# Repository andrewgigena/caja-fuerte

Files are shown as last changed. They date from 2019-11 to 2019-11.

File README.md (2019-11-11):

# 1. Introducción

La idea detrás del proyecto, recae en la necesidad moderna de proteger
información muy valiosa y confidencial. Para que esta información no
termine en manos de personas que no deberían tener acceso en primer
lugar, se busca crear un modelo eficiente, seguro y confiable para la
protección de datos, garantizando al usuario que sus datos u objetos
serán protegidos.

Por ese motivo llegamos a la idea de elaborar una caja fuerte a la que
se pueda tener acceso mediante una contraseña. Esta misma será elaborada
por el propietario y podrá ser cambiada a gusto siempre que lo disponga.
Además de la contraseña de usuario, la caja fuerte tendrá una contraseña
maestra que quedará en las manos de la empresa (grupo del proyecto) para
poder acceder a el interior de la caja en caso de: una contraseña
olvidada por el usuario y fallas en el sistema que necesiten un
reajuste.

La caja dispondrá de una alarma que se activará al ser introducida una
contraseña errónea un total de tres veces alertando al dueño sobre la
situación de sus pertenencias.

## 2. Contenido:
### 2.1. Descripción abreviada del contenido del proyecto

Una caja fuerte accesible mediante una contraseña creada por el
propietario. La programación se ejecutara mediando Arduino, además se
dispondrá de una pequeña pantalla que facilitara al usuario la
interacción con el software de seguridad y una alarma para más seguridad
tratando de cubrir todas las áreas posibles que brinden seguridad a lo
que se quiera guardar en ella.

### 2.2. Integrantes del equipo
Los integrantes pertenecientes al grupo 3º BG serán los siguientes:
Andrew Gigena, Gastón Cabrera y Richard Correa.

### 2.3. Asignaturas involucradas
Las asignaturas involucradas hasta ahora serán analógica y digital, en
el desarrollo del proyecto se evaluara la idea de incluir más materias o
simplemente dejar las ya involucradas.

### 2.4. Cronología del proyecto
En el comienzo del proyecto se pensó en utilizar tres sistemas de
seguridad: protección por huella dactilar, contraseña digital mediante
el teclado y una llave física.

Como computadora central de la caja fuerte utilizamos una Arduino debido
a la versatilidad y tamaño reducido de la misma. Además de que permite
modificar su funcionamiento sobre la marcha.

Tras investigar el coste de los módulos disponibles de huellas
dactilares para Arduino, la idea de utilizar este método de seguridad
fue descartada por exceso de coste.

Entonces esperábamos utilizar la llave física y la contraseña digital,
pero por inconvenientes que mencionaremos más adelante, tuvo que
descartarse la llave física.

Cuando finalizamos que sistema utilizar, nos pusimos manos a la obra con
el diseño de la caja fuerte. Para la construcción de la caja primero se
pensó qué materiales utilizar, en un principio se pensó hacerlo de metal
porque tomamos como referencia los diseños existentes en el mercado.
Pero luego de analizar los costos descubrimos que era mejor utilizar
madera compensada. Tras eso se pensó en la forma de unir las paredes de
la misma y llegamos a la conclusión de unirlas con doce ángulos de
metal.

El lugar donde decidimos comprar los materiales fue en la sucursal de
Sodimac por la proximidad del lugar. En este fue comprado las seis
tablas de madera, que se utilizarían para los lados de la caja y se
compró el doble fondo que es una madera más fina que la de los lados.
También los doce ángulos para unir las maderas previamente mencionados.

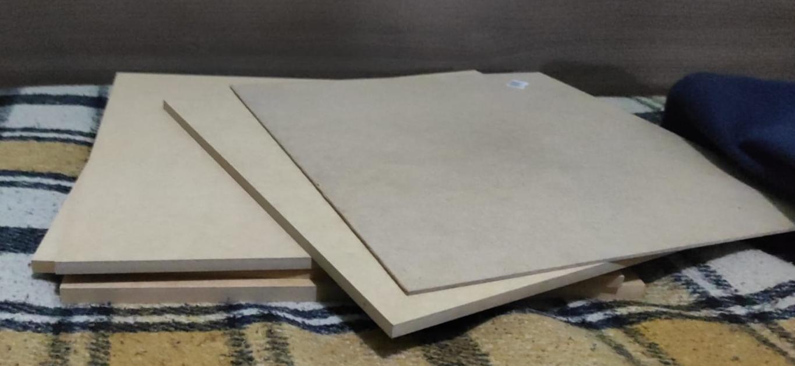
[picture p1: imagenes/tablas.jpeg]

<p align="center"><b>Figura 1. Seis tablas y la tabla del doble fondo</b></p>

Una vez obtenidos los materiales pasamos a construir la caja fuerte.
Primero fue construido el piso y los tres laterales principales. Dejando
a propósito la puerta y el techo para facilitar el acceso y colocación
de los componentes.

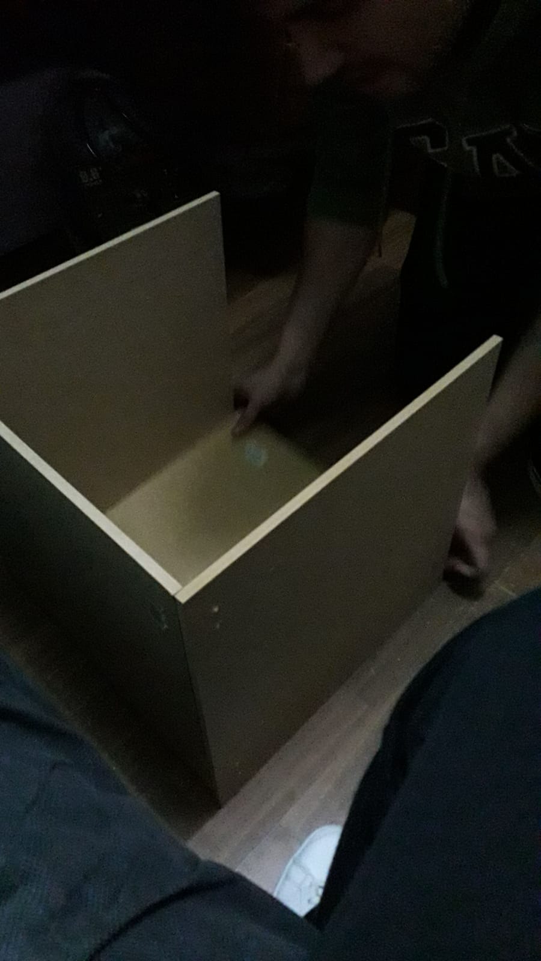
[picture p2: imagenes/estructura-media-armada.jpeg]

<p align="center"><b>Figura 2.  Estructura Inicial</b></p>

En el lapso de dos semanas, investigamos que componentes comprar para
comenzar a programar el proyecto. Fuimos comprando por partes y
avanzando en la programación de ese componente, a pesar de no tener
físicamente el mismo.

Se comenzó utilizando una Arduino Uno para realizar todo el desarrollo,
pero pronto se hizo evidente que el numero de pines seria un problema
para controlar tantos componentes simultáneamente. Por eso se decidió
comprar dos Arduino Mega, una clásica que se utilizaba para realizar
pruebas y otra de tamaño reducido pensada para ser soldada.

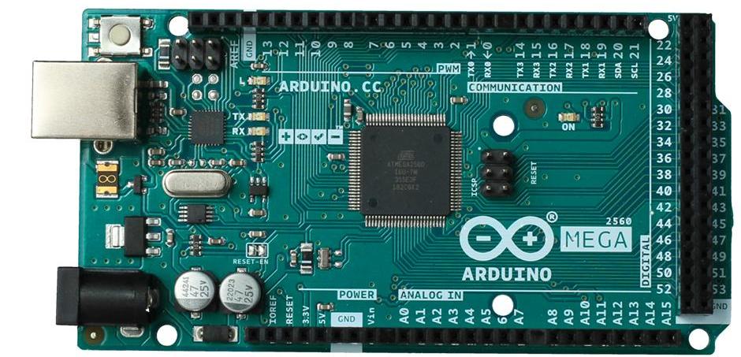
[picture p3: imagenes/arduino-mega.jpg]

<p align="center"><b>Figura 3.  Arduino Mega Clásica</b></p>

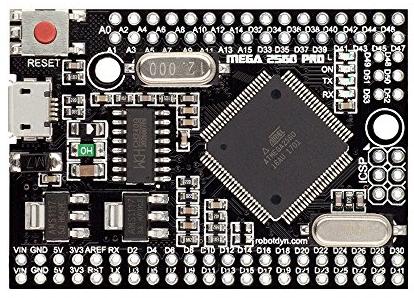
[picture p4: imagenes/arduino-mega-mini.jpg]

<p align="center"><b>Figura 4.  Arduino Mega Mini</b></p>

Durante la espera de los envíos internacionales, fue diseñada y
ensamblada la placa con la iluminación led que se encargara de mostrar
los intentos disponibles, y si la caja estaba abierta o cerrada.


<p align="center"><b>Figura 5.  Iluminación de ledes</b></p>

Mientras se buscaba un teclado acorde al proyecto, se hizo uno de
prueba, tras la compra del teclado de membrana su implementación a la
caja fue inmediata.


<p align="center"><b>Figura 6.  Teclado de prueba</b></p>

Tras solucionar el asunto de la Arduino, continuamos con modelado de la
caja. Nos enfocamos en el calado de la puerta donde iría la pantalla y
los ledes. Las medidas del calado de la pantalla son de 7.5 x 2.5cm,
luego los orificios de los ledes los hicimos con una mecha de 7mm, el
calado de la puerta lo hicimos con un cincel.

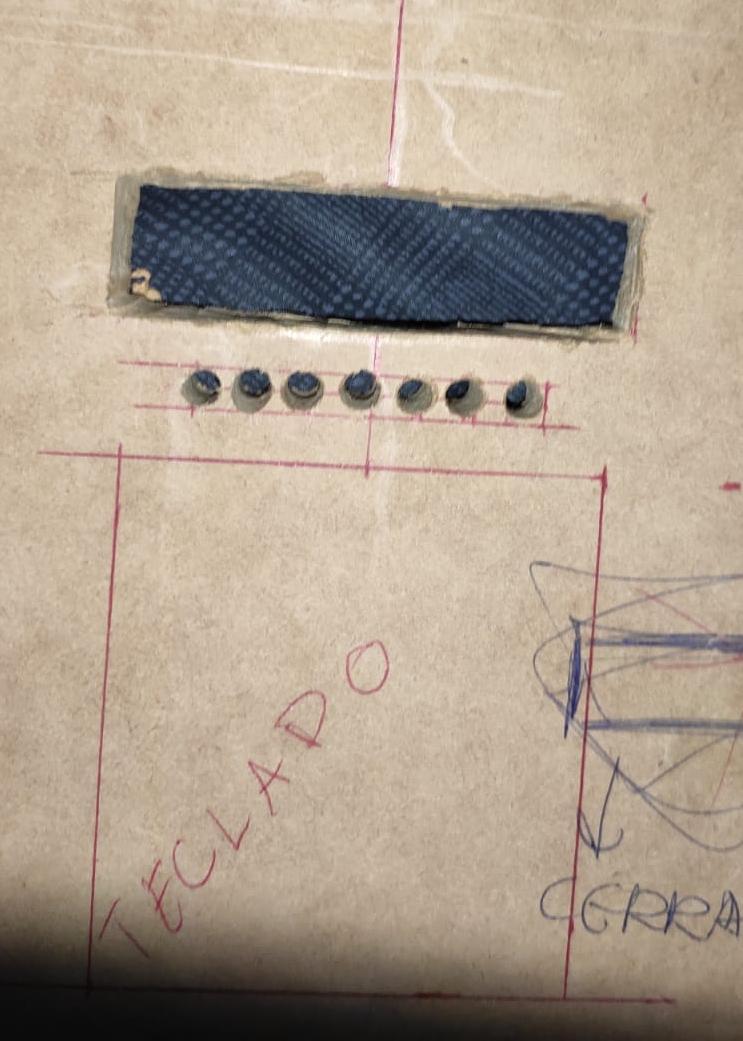
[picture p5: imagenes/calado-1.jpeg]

<p align="center"><b>Figura 7.  Calado de Ledes/Pantalla</b></p>

Aquí es cuando notamos un error que nos llevo a descartar la llave
física, que impedía la colocación de la cerradura y perjudicaba la
estructura de la puerta.

Dentro de las compras tanto locales como internacionales, se encuentra
la pantalla, pensada como el medio principal de interacción que tendría
el usuario con el sistema.

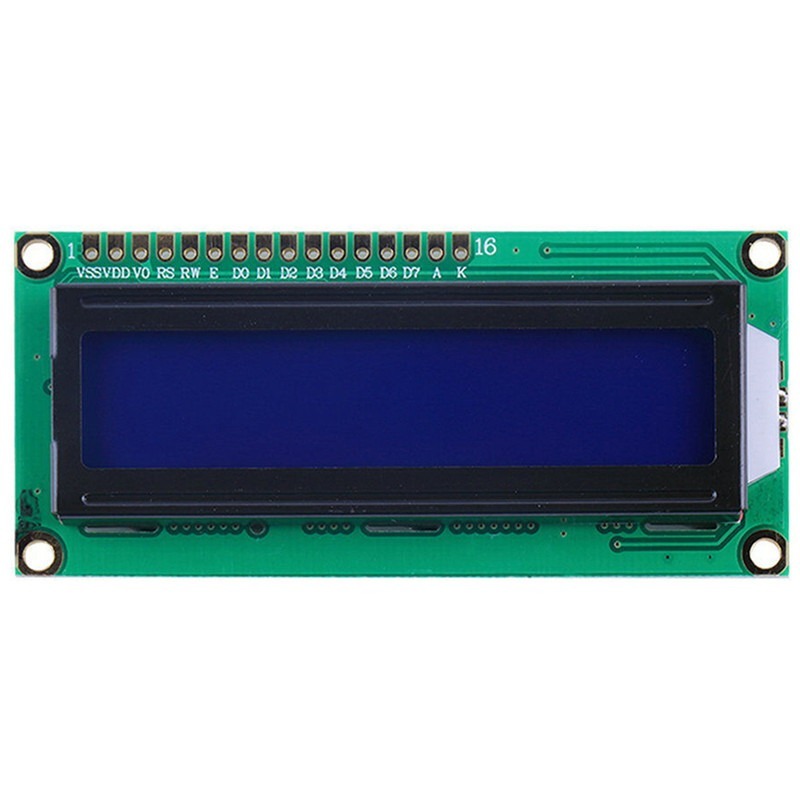
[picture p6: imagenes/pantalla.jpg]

<p align="center"><b>Figura 8.  Pantalla LCD</b></p>

El teclado de membrana previamente mencionado como suplente al teclado
de botones.


<p align="center"><b>Figura 9.  Teclado de membrana</b></p>

Luego fue comprada la cerradura para comprobar que el orificio de la
cerradura en la puerta coincidiera, luego de llegar a un diseño
satisfactorio, fue implementado el código de la cerradura que seria
controlado por un relé.


<p align="center"><b>Figura 10. Cerradura Electromagnetica</b></p>

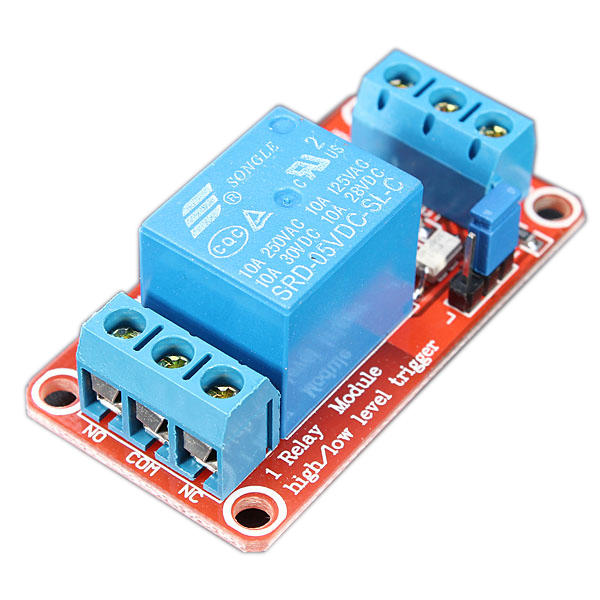
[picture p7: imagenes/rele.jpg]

<p align="center"><b>Figura 11. Relé</b></p>

Cuando todos los componentes estaban físicamente disponibles, realizamos
todas las pruebas de código y terminamos la puerta, fueron colocados
todos los componentes en la puerta para ser soldados y/o
interconectados.

Una vez realizado el calado en la puerta faltante y la colocación de los
componentes en la misma, procedimos a ensamblarla en la estructura.

Decidimos que la puerta quedaría colocada entre los laterales de la
caja. Para hacer esto, utilizamos dos bisagras, qué estarían colocados a
la derecha de la caja fuerte, una vez colocada la puerta procedimos a
colocar el asa, que mejor se acoplaba al diseño de la caja fuerte.
Colocamos el techo de la caja fuerte del mismo modo que colocamos los
laterales y el piso. Se hizo un calado dónde iría la entrada de
corriente, ubicada en la parte posterior de la caja y agujeros donde
estarían ubicados los parlantes de la alarma, estos últimos fueron
hechos con una mecha de 5mm.

Colocamos la entrada de corriente de 230v interconectada a una fuente
conmuta de 20v, en la salida de esta fue conectado un regulador de
voltaje LM317 para bajar el voltaje a 12v.

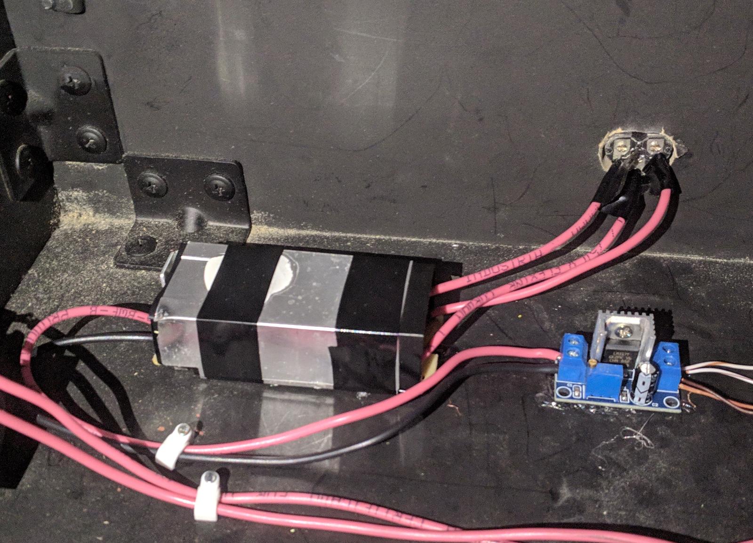
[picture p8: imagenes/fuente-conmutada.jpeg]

<p align="center"><b>Figura 12. Fuente Conmutada y Regulador de Voltaje</b></p>

***Falta el amplificador y el rele del mismo***

La caja fuerte fue pintada progresivamente mientras se avanzaba e la
misma. El color escogido fue negro mate ya que notamos que era el color
más frecuente en el mercado de las cajas fuertes, para que luzca más
estético y profesional.


<p align="center"><b>Figura 13. Caja Fuerte terminada</b></p>

### 2.5 Complicaciones durante en producción
---------------
#### 2.5.1 Complicaciones en la programación

Durante la programación, fue necesario utilizar la EEPROM de manera
obligatoria, cada vez que inicia la caja comprueba diferentes valores
para impedir el uso o saltarse la programación para abrir la puerta.

\
Otra dificultad que ocurrió durante la programación fue impedir todos
los errores que imposibilitarían el inicio o continuación de la misma.
Eso fue realizado mediante distintos modos internos que el programa
accedería, por ejemplo el modo de nuevo pin. Este modo que se accede con
el único propósito de cambiar el pin actual o fijar uno inicial.

Los modos internos utilizados por el programa son los siguientes:

-   **Modo Alarma:** La alarma comienza a sonar y el usuario/empleado de
    la empresa debe colocar el código puk para desactivar la alarma y
    volver al Modo Ingreso de Pin
-   Modo Nuevo Pin: A través del teclado permite ingresar un pin que se
    guardara en la EEPROM como el pin almacenado. El usuario puede
    aceptar el pin que ingreso o volver a ingresar otro.
-   **Modo Ingreso de Pin:** El usuario debe ingresar el pin de seis
    dígitos. Tras confirmar, el sistema compara el pin ingresada con el
    pin almacenado, si la contraseña es correcta el sistema entra en el
    Modo Caja Abierta. Si en cambio, el pin es incorrecto restaría un
    intento y desactivaría un led de intentos. Cuando los intentos son
    iguales a cero el sistema se bloqueara para entrar en el Modo
    Alarma.
-   **Modo Caja Abierta:** Al iniciar este modo toma el tiempo de inicio
    para calcular posteriormente que hayan transcurrido cinco minutos.
    Pasados estos cinco minutos la cerradura automáticamente se
    cerraría. A pesar de esto, el usuario puede cerrar a voluntad la
    cerradura y cambiar el pin
-   Modo Programador: Permite modificar aspectos de la caja a traves de
    comandos especiales. Estos comandos son desactivar/activar la
    alarma, desactivar/activar cerradura, desactivar/activar primer
    inicio.

#### 2.5.2 Complicaciones de ensamblaje

Mientras realizamos la construcción de la caja obtuvimos una serie de
problemas, estos problemas fueron:

-   Al colocar las bisagras en la puerta, esta no se abría
    completamente. Por eso nos vimos obligados a alterar un poco el
    diseño de la misma, la solución que encontramos a este problema fue
    agregarle un complemento al lateral donde iban las bisagras y
    también sé lijo un ángulo de la puerta. Estos cambios son para
    mejorar la apertura de la puerta.

-   Otro de los problemas que tuvimos fue en la parte de la colocación
    de los laterales ya que la madera era compensada y al colocar los
    tornillos no apretaban lo suficiente. Este problema lo solucionamos
    con unos tornillos que se acoplan mejor a la madera compensada y
    también se trató de no quitar los tornillos una vez colocado en la
    madera.
-   El calado de la pantalla tuvo que ser movido unos centímetros hacia
    arriba, porque la pantalla y la iluminación led se solapaban las
    placas e impedía colocarlos correctamente.

Durante la colocación de los componentes tuvimos problemas con la
sección de los cables, estos cables se partieron y que tuvieron que ser
resoldados.

#### 2.5.3 Complicaciones en la soldadura

Se utilizo un estaño de mala calidad durante el comienzo de la
soldadura, con un alto grado de plomo. Esto nos obligo a cambiar por un
estaño de más calidad.

También tuvimos un cortocircuito que daño la pantalla LCD, este fue
producido por cables multifilares mal soldados, algo que nos obligo a
comprar otra y repensar como conectar las soldaduras para que no ocurra
lo mismo.

Al final notamos que una gota de estaño cayo en los pines del ATMEGA
2560 de la Arduino Mega, y tuvo que ser resoldado el chip SMD con mucho
cuidado para evitar cortocircuitar el integrado.

# 3. Comportamiento del sistema

## 3.1 Diagrama de bloques:
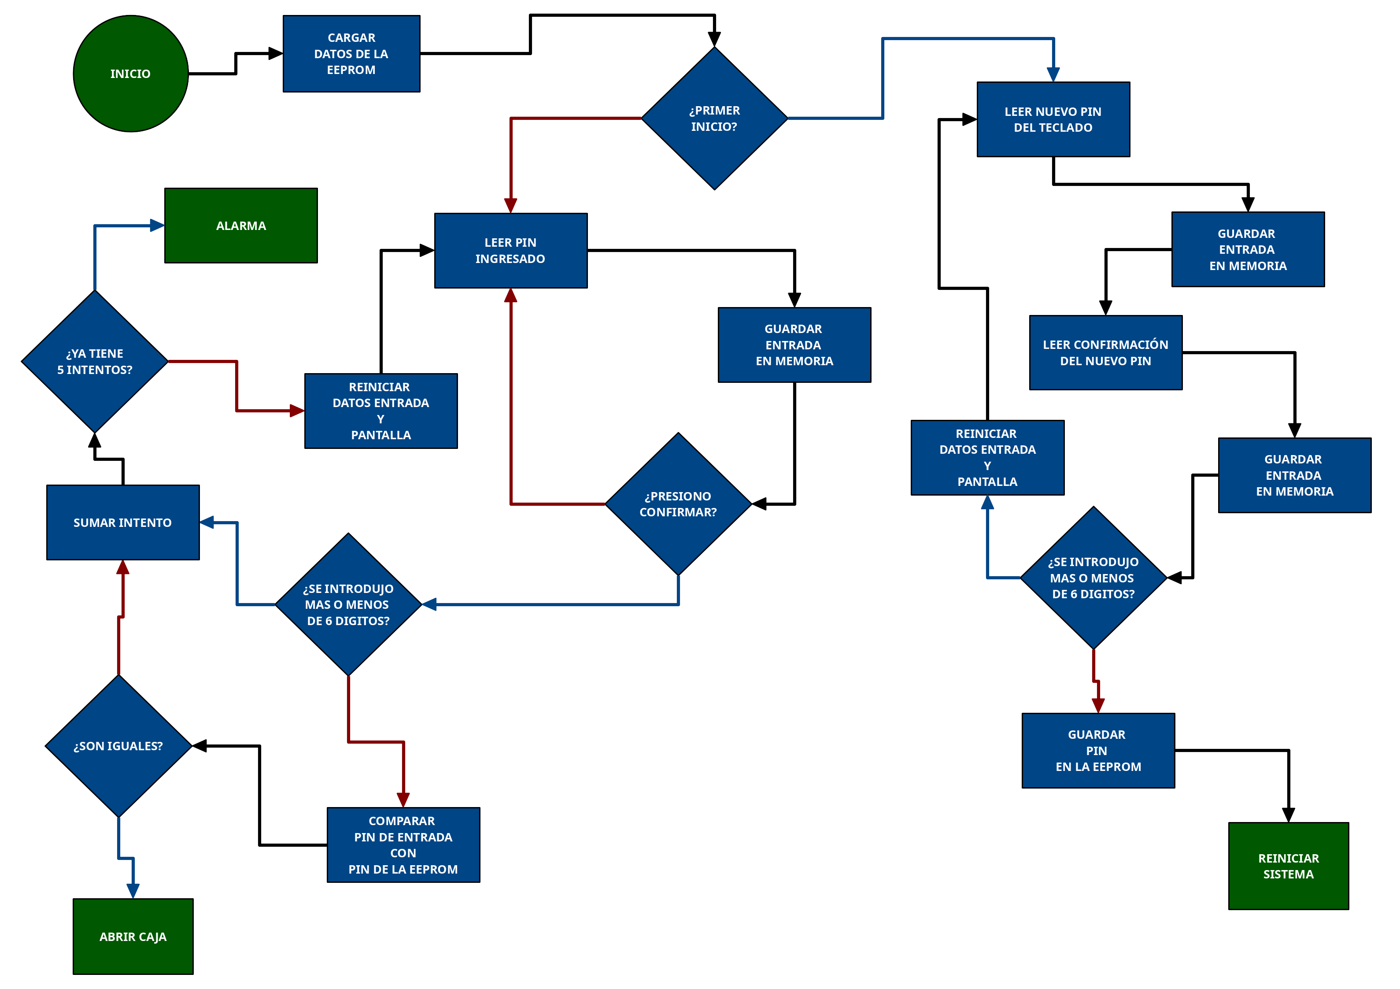
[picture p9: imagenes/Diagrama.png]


## 3.2 Comportamiento Funcional:
El programa dispone de dos modos principales, el modo usuario donde se
realizara casi todas las operaciones y el modo programador/empresa donde
hacen cambios de pruebas/funcionamientos.

### 3.2.1 Modo usuario:

Al inicio del sistema este comprueba si este es el primer inicio del
mismo. Si la respuesta es positiva, pide un nuevo pin de seis dígitos al
usuario. Luego pide una confirmación de la misma para guardar en la
EEPROM o reingresar otra contraseña distinta. En el caso de tener un pin
ya designado, se deberá ingresar el misma para acceder al interior de la
caja.

El usuario tiene cinco intentos para ingresar correctamente el pin
guardado, donde por cada intento fallido se apagará uno de los ledes de
intentos. En el caso de ocurrir cinco intentos fallidos, se encenderá un
led encendido de color rojo y se activara una alarma para alertar al
usuario de un posible intruso. La alarma seguirá activa hasta que la
empresa o el usuario ingrese el código puk.

En caso de ingresar el pin correcto, se encenderá un led de color verde,
se reinicia el número de intentos disponibles a cinco, y se accionara la
cerradura para tener el acceso a la caja fuerte.

Tras acceder a la caja fuerte, el usuario podrá almacenar o retirar el
contenido del mismo. También podrá cambiar la contraseña actual y/o
cerrar la puerta manualmente. Aun así está habilitado un sistema de
cerrado automático tras cinco minutos

### 3.2.2 Modo programador:

En este modo es accesible mediante a una pin especial que solo tendrá
conocimiento la empresa, en este modo se podrá: Tanto activar o
desactivar la alarma, abrir o cerrar la caja y cambiar la contraseña del
usuario, luego de finalizado estos procedimientos se saldrá del modo
programador para ingresar nuevamente al modo usuario, donde se activarán
la funciones asignadas.

# 4. Descripción de los componentes

## 4.1. Arduino Mega

## 4.2. Teclado
El teclado utilizado es uno de membrana de 12 botones en una
organización de 4 filas x 3 columnas. Es muy utilizado con las placas de
desarrollo Arduino, sensible al tacto por lo cual no se requiere una
gran presión para activar las teclas lo cual lo vuelve muy cómodo, la
ventaja de este teclado es que al tener una conexión flexible puede ser
colocado en cualquier superficie sin problemas.

## 4.3. Parlantes
Se utilizaron dos parlantes de 4Ω en serie, debido a que era lo
que más nos convenía en relación tamaño y potencia. Este dispositivo
esta destinado a la conversión de ondas eléctricas en energía mecánica
y de mecánica en acústica. Es por tanto la puerta por donde sale el
sonido al exterior desde los aparatos que posibilitaron su
amplificación.

## 4.4. Cerradura
Se utilizo esta cerradura por su tamaño reducido y voltaje ya que se
acciona con 12v. Este voltaje es compatible con el amplificador que
utiliza 12v algo conveniente para el proyecto. La cerradura está
compuesto por un solenoide, que es básicamente un electromagneto.

Estos están hechos de una gran bobina de alambre con una armadura (un
lingote de metal) en el medio. Cuando la bobina es energizada, el
lingote es tirado al centro de la bobina. Esto hace que el solenoide sea
capaz de empujar hasta el final de la cerradura.

Normalmente el lingote está expandido por lo tanto no puedes abrir la
puerta porque obstruye el camino. No usa ninguna potencia extra en este
estado. Cuando son aplicados 9-12VDC, el lingote se retrae por lo que no
sobresale más y la puerta puede ser abierta. Los solenoides vienen con
un lingote inclinado como se muestra, pero puedes abrirlo con los dos
tornillos de cabeza Philips y rotarlo 180 grados, por lo que podrán
coincidir con la puerta que quieras usarlos.

## 4.5. Pantalla
Utilizamos esta pantalla por ser muy compatible con la Arduino debido a
las librerías y ejemplos ya existentes. Esta pantalla es de 16x02
caracteres y opera con un voltaje de 5v. Tiene una interfaz paralela de
4 u 8 bits, nosotros utilizamos la segunda interfaz. Su color de texto
es blanco y la luz de fondo es de color azul.

## 4.6. Regulador de Voltaje
Utilizamos un regulador de voltaje porque la fuente es de 20v y
necesitamos reducir a 12v debido a que nuestro circuito funciona a este
voltaje. Para ello utilizamos un LM317, qué permite regular el voltaje
de entrada hacia un máximo de 1.5A y 37V de salida.

## 4.7. Amplificador
Usamos un amplificador de audio de 18w para el funcionamiento de los
parlantes de la alarma, ya que este era necesario para mejorar la
potencia del audio ya que sin el mismo, el sonido era muy bajo. Este
amplificador utiliza un TDA2030 cuyo rango de operación es de 6v a 18v,
y la salida al parlante de 4Ω a 8Ω

## 4.8. Relés
Se utilizo un relé de 5v porque era compatible con el Arduino y permite
cambiar la polaridad de normalmente cerrado (NC) al normalmente abierto
(NA). Los relés son dispositivos electromagnéticos. Funciona como un
interruptor controlado por un circuito eléctrico en el que, por medio de
una bobina y un electro imán, se acciona un juego de uno o varios
contactos que permiten abrir o cerrar otros circuitos eléctricos
independientes.

## 4.9. Iluminación de Ledes

# 5. Cotización del Proyecto
Las estimaciones de costes que tuvimos al comienzo del proyecto eran de
8500 $U, pero tras comprar todo y armarlo, el presupuesto final fue de
7320 $U, porque algunos productos los trajimos desde el extranjero.
  
 Cantidad | Material                           | Precio
--------- | ---------------------------------- | ---------
  1       | Cerradura electromagnética de 12v  | 1300 $U
  1       | Teclado de 4x3 botones             |  130 $U
  2       | Parlantes de 4Ω                    |  GRATIS
  1       | Arduino Mega 2560 Pro Embedded     |  330 $U
  1       | Pantalla LCD 1602A                 |  240 $U
  1       | Placas de prototipo de puntos      |  GRATIS
  1       | Relé de 5v Control, 220AC Salida   |  160 $U
  4       | 10 metros de cables de 0.5mm       |  320 $U
  7       | Tablones de 40cm x 40cm            | 1120 $U
  2       | Bisagras de hierro                 |   80 $U
  12      | Ángulos de Juntura                 |  720 $U
  2       | Aerosoles de Pintura               |  920 $U
  1       | Rollo de Estaño                    | 1600 $U
  1       | Pestillo                           |   80 $U

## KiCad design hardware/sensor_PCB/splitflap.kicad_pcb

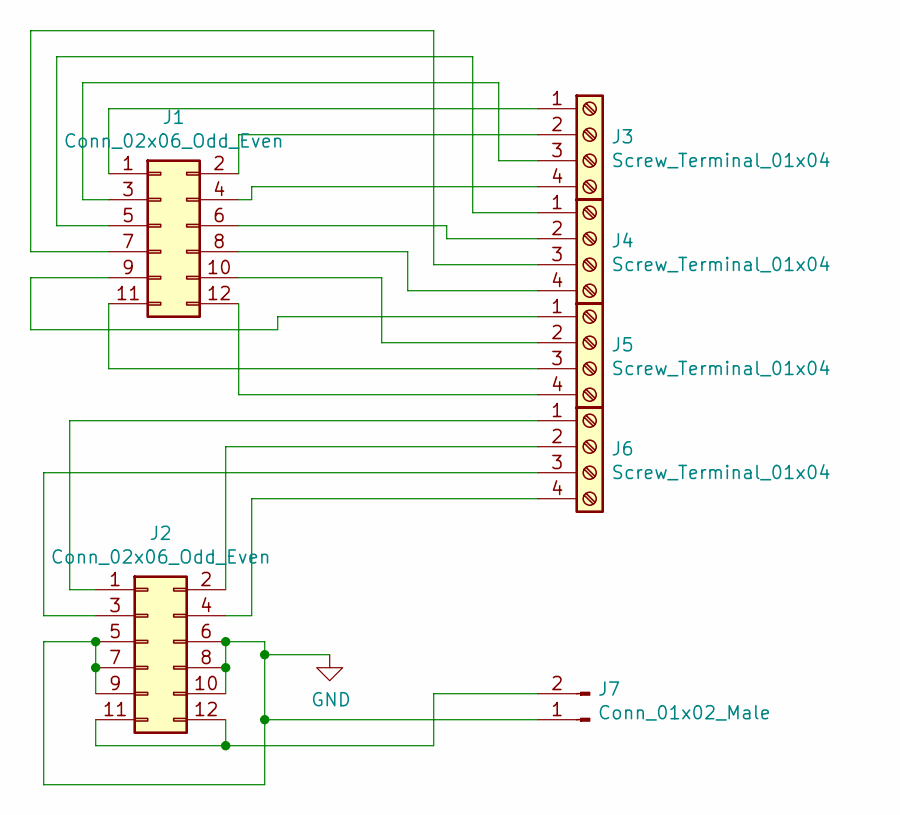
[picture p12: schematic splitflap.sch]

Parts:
J1, J2: Conn_02x06_Odd_Even; IDC-Header_2x06_P2.54mm_Vertical
J3, J4, J5, J6: Screw_Terminal_01x04; TerminalBlock_bornier-4_P5.08mm
J7: Conn_01x02_Male; JST_EH_B2B-EH-A_1x02_P2.50mm_Vertical

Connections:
GND: J2.5, J2.6, J2.7, J2.8, J2.9, J2.10, J7.1
unnamed: J1.1, J3.1
unnamed: J1.2, J3.2
unnamed: J1.3, J3.3
unnamed: J1.4, J3.4
unnamed: J1.5, J4.1
unnamed: J1.6, J4.2
unnamed: J1.7, J4.3
unnamed: J1.8, J4.4
unnamed: J1.9, J5.1
unnamed: J1.10, J5.2
unnamed: J1.11, J5.3
unnamed: J1.12, J5.4
unnamed: J2.1, J6.1
unnamed: J2.2, J6.2
unnamed: J2.3, J6.3
unnamed: J2.4, J6.4
unnamed: J2.11, J2.12, J7.2

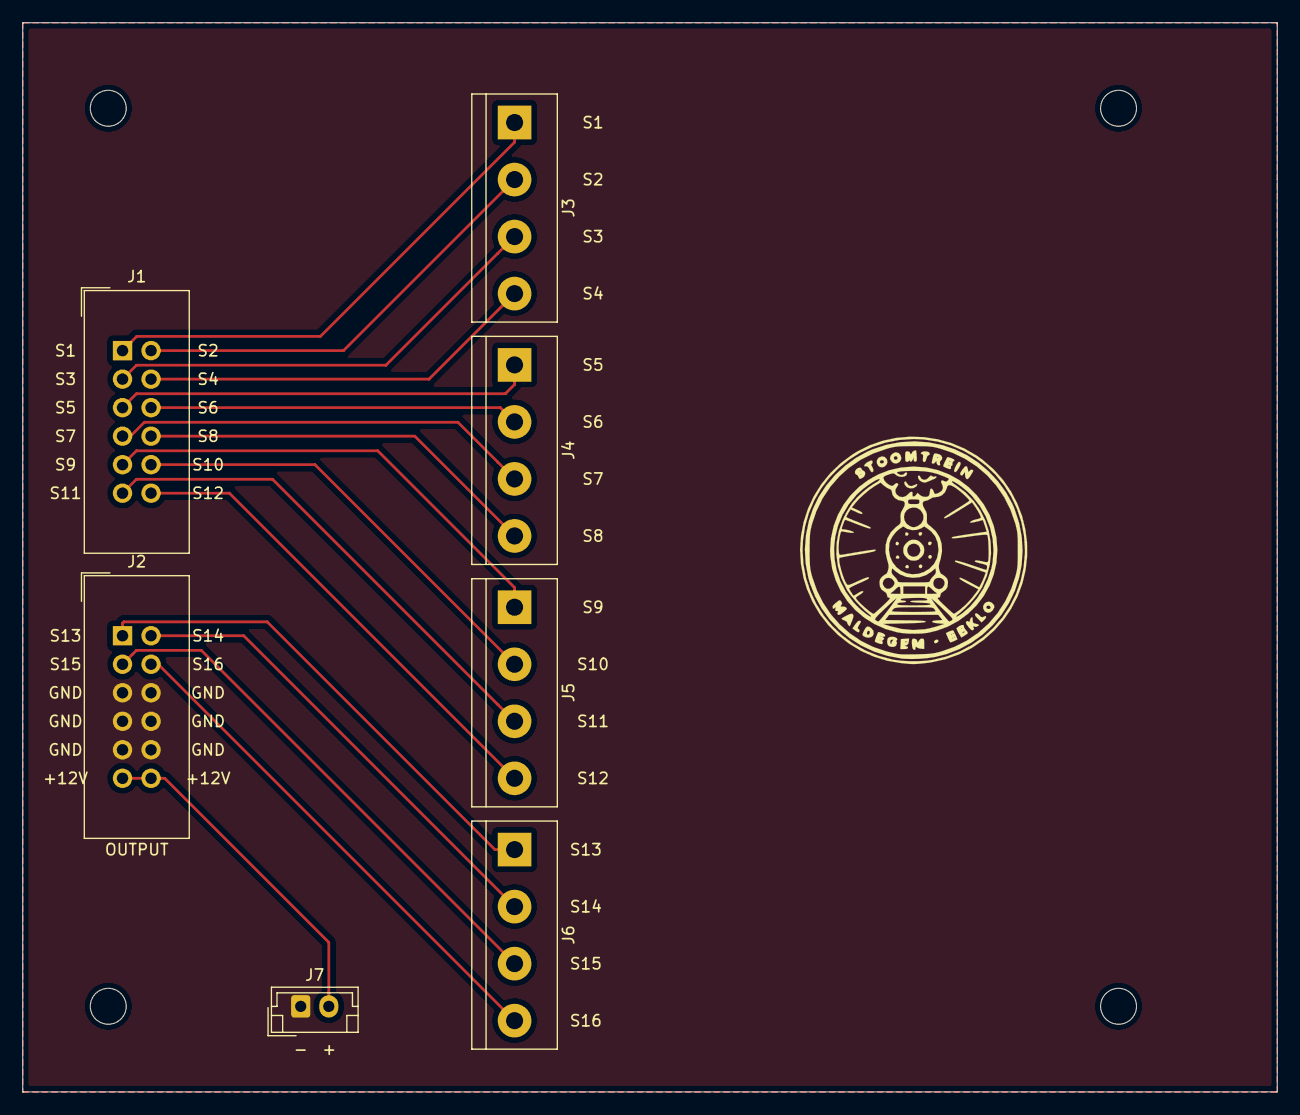
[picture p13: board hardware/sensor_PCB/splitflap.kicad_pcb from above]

Board: 2 copper layers, 111.8 x 95.2 mm, 7 parts (0 on the bottom side), 18 nets.

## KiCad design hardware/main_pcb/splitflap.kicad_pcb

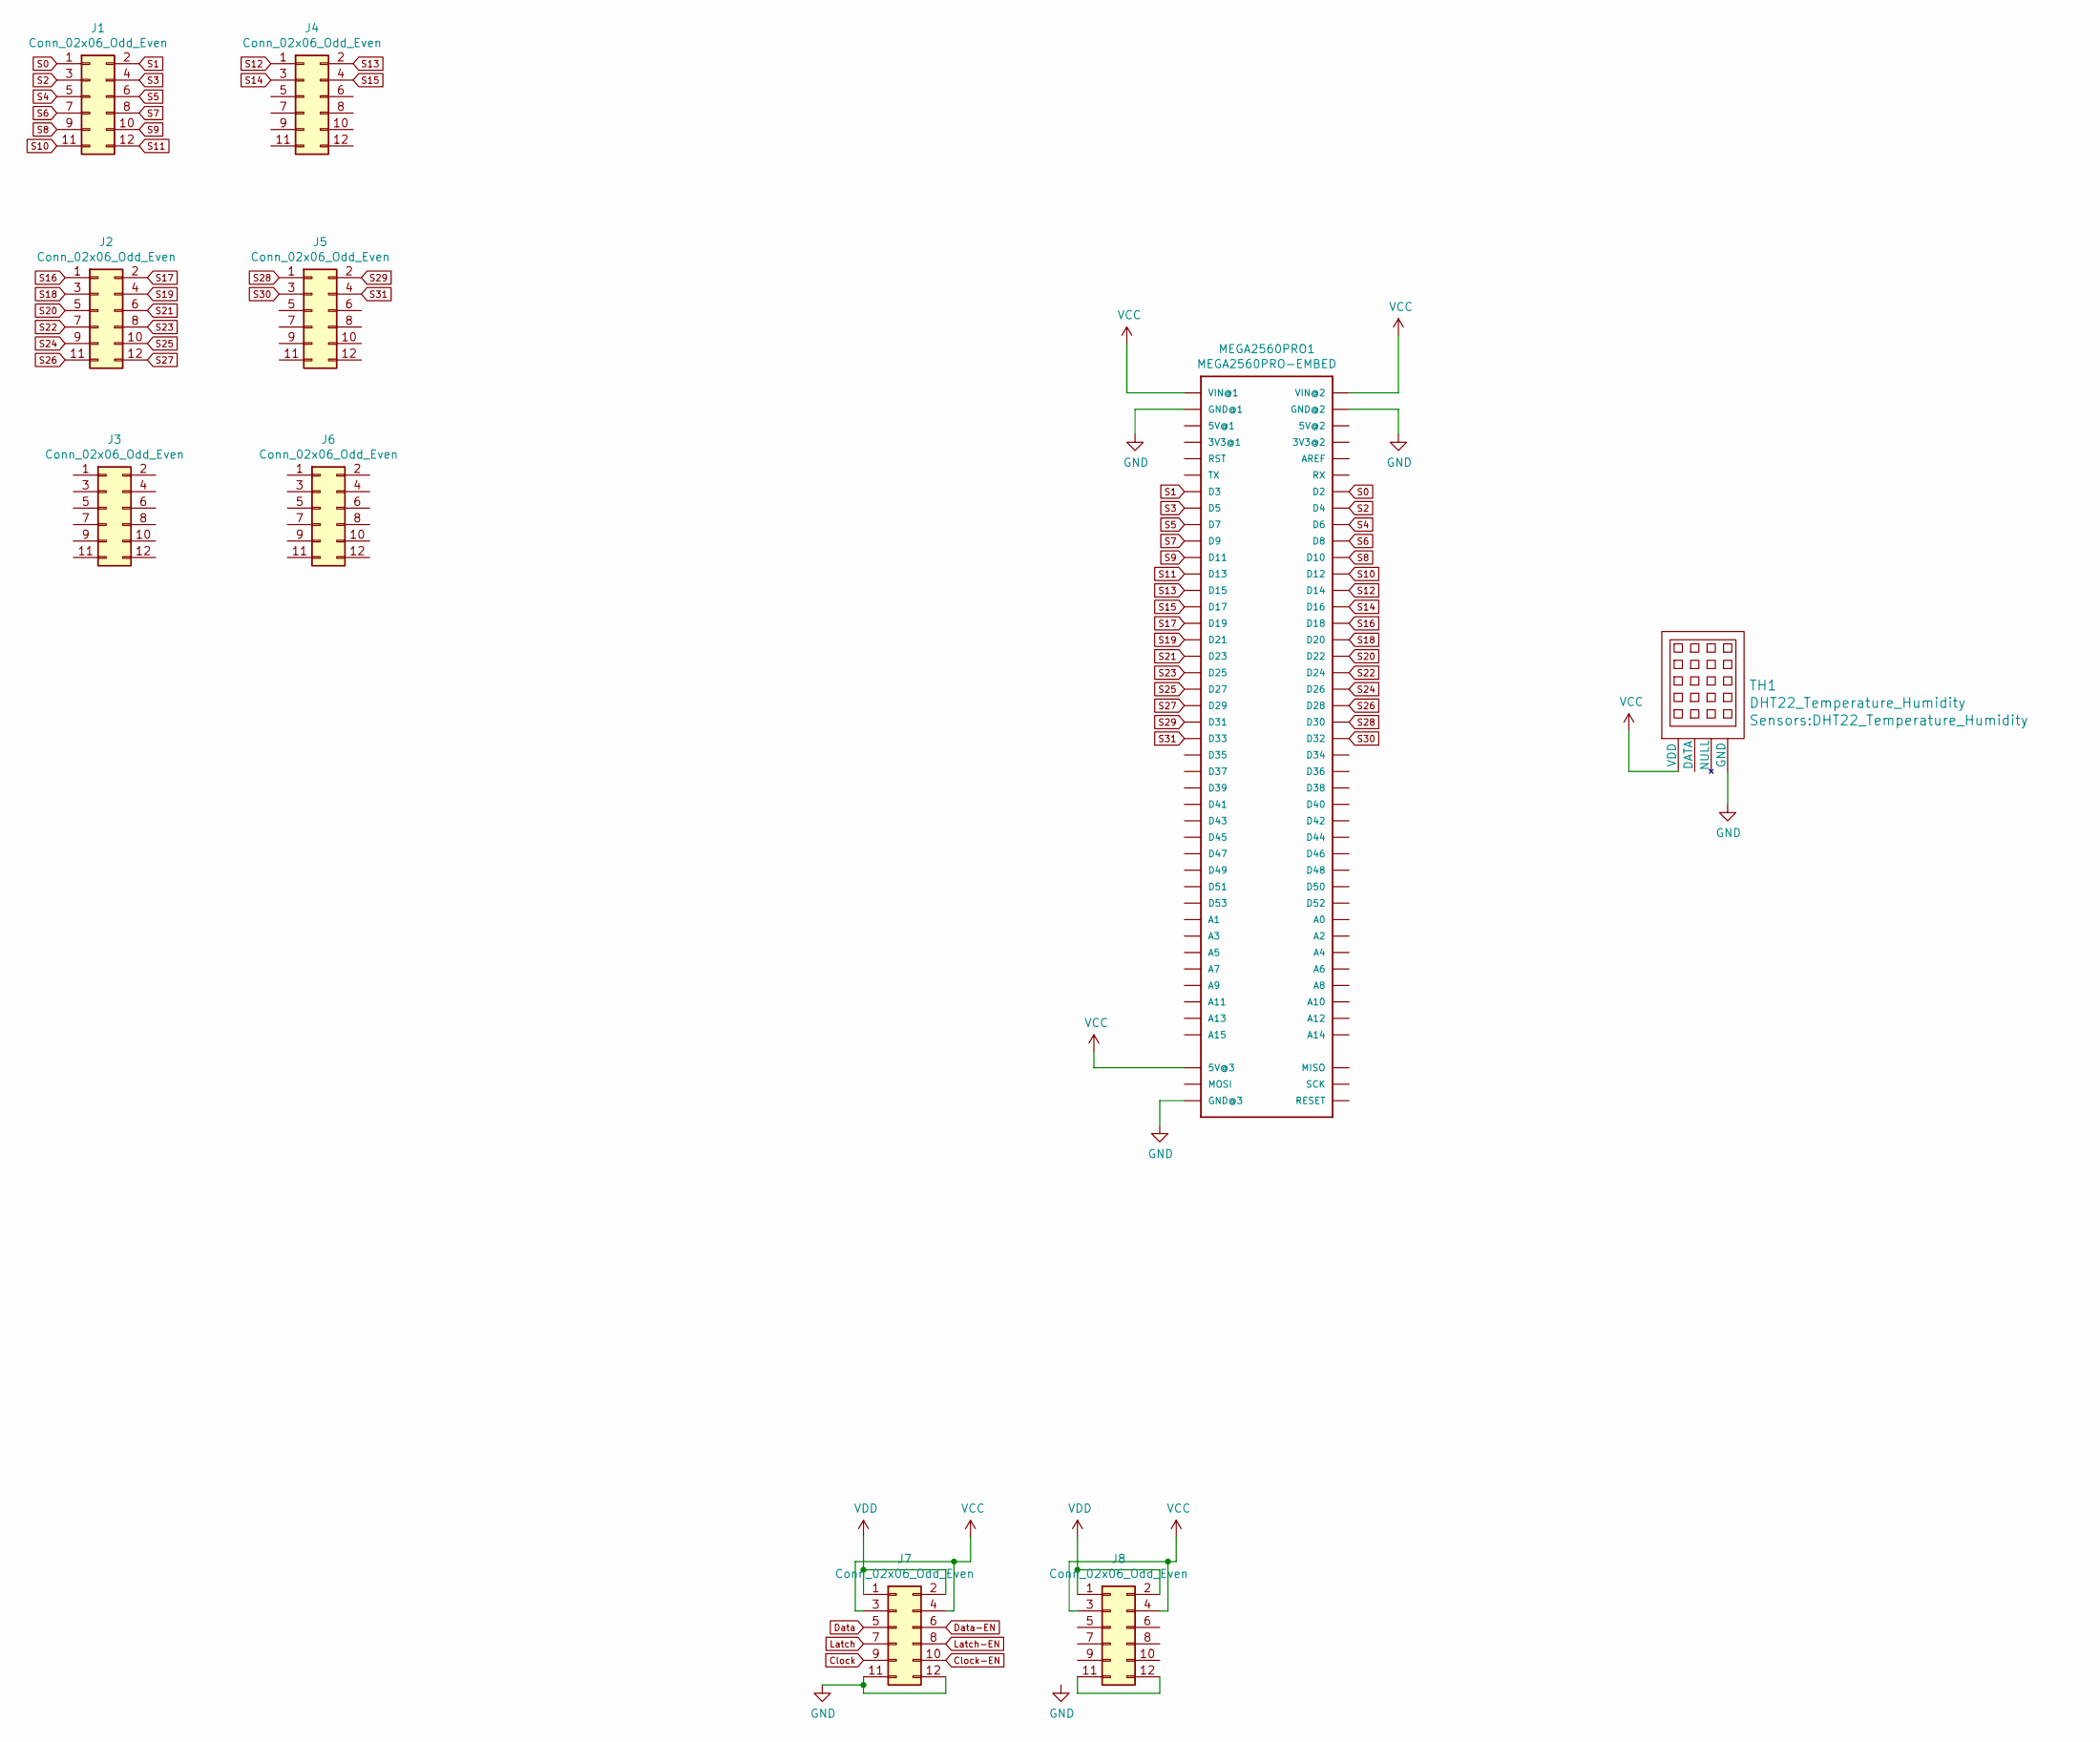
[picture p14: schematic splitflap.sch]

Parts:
J1, J2, J3, J4, J5, J6, J7, J8: Conn_02x06_Odd_Even; IDC-Header_2x06_P2.54mm_Vertical
MEGA2560PRO1: MEGA2560PRO-EMBED
TH1: DHT22_Temperature_Humidity

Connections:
Clock: J7.9
Clock-EN: J7.10
Data: J7.5
Data-EN: J7.6
GND: J7.11, J7.12, MEGA2560PRO1.GND@1, MEGA2560PRO1.GND@2, MEGA2560PRO1.GND@3, TH1.4 (GND)
Latch: J7.7
Latch-EN: J7.8
unnamed: J8.11, J8.12
S0: J1.1, MEGA2560PRO1.D2
S1: J1.2, MEGA2560PRO1.D3
S2: J1.3, MEGA2560PRO1.D4
S3: J1.4, MEGA2560PRO1.D5
S4: J1.5, MEGA2560PRO1.D6
S5: J1.6, MEGA2560PRO1.D7
S6: J1.7, MEGA2560PRO1.D8
S7: J1.8, MEGA2560PRO1.D9
S8: J1.9, MEGA2560PRO1.D10
S9: J1.10, MEGA2560PRO1.D11
S10: J1.11, MEGA2560PRO1.D12
S11: J1.12, MEGA2560PRO1.D13
S12: J4.1, MEGA2560PRO1.D14
S13: J4.2, MEGA2560PRO1.D15
S14: J4.3, MEGA2560PRO1.D16
S15: J4.4, MEGA2560PRO1.D17
S16: J2.1, MEGA2560PRO1.D18
S17: J2.2, MEGA2560PRO1.D19
S18: J2.3, MEGA2560PRO1.D20
S19: J2.4, MEGA2560PRO1.D21
S20: J2.5, MEGA2560PRO1.D22
S21: J2.6, MEGA2560PRO1.D23
S22: J2.7, MEGA2560PRO1.D24
S23: J2.8, MEGA2560PRO1.D25
S24: J2.9, MEGA2560PRO1.D26
S25: J2.10, MEGA2560PRO1.D27
S26: J2.11, MEGA2560PRO1.D28
S27: J2.12, MEGA2560PRO1.D29
S28: J5.1, MEGA2560PRO1.D30
S29: J5.2, MEGA2560PRO1.D31
S30: J5.3, MEGA2560PRO1.D32
S31: J5.4, MEGA2560PRO1.D33
VCC: J7.3, J7.4, J8.3, J8.4, MEGA2560PRO1.5V@3, MEGA2560PRO1.VIN@1, MEGA2560PRO1.VIN@2, TH1.1 (VDD)
VDD: J7.1, J7.2, J8.1, J8.2

Board: 2 copper layers, 10 parts (0 on the bottom side), 36 nets, no tracks yet.

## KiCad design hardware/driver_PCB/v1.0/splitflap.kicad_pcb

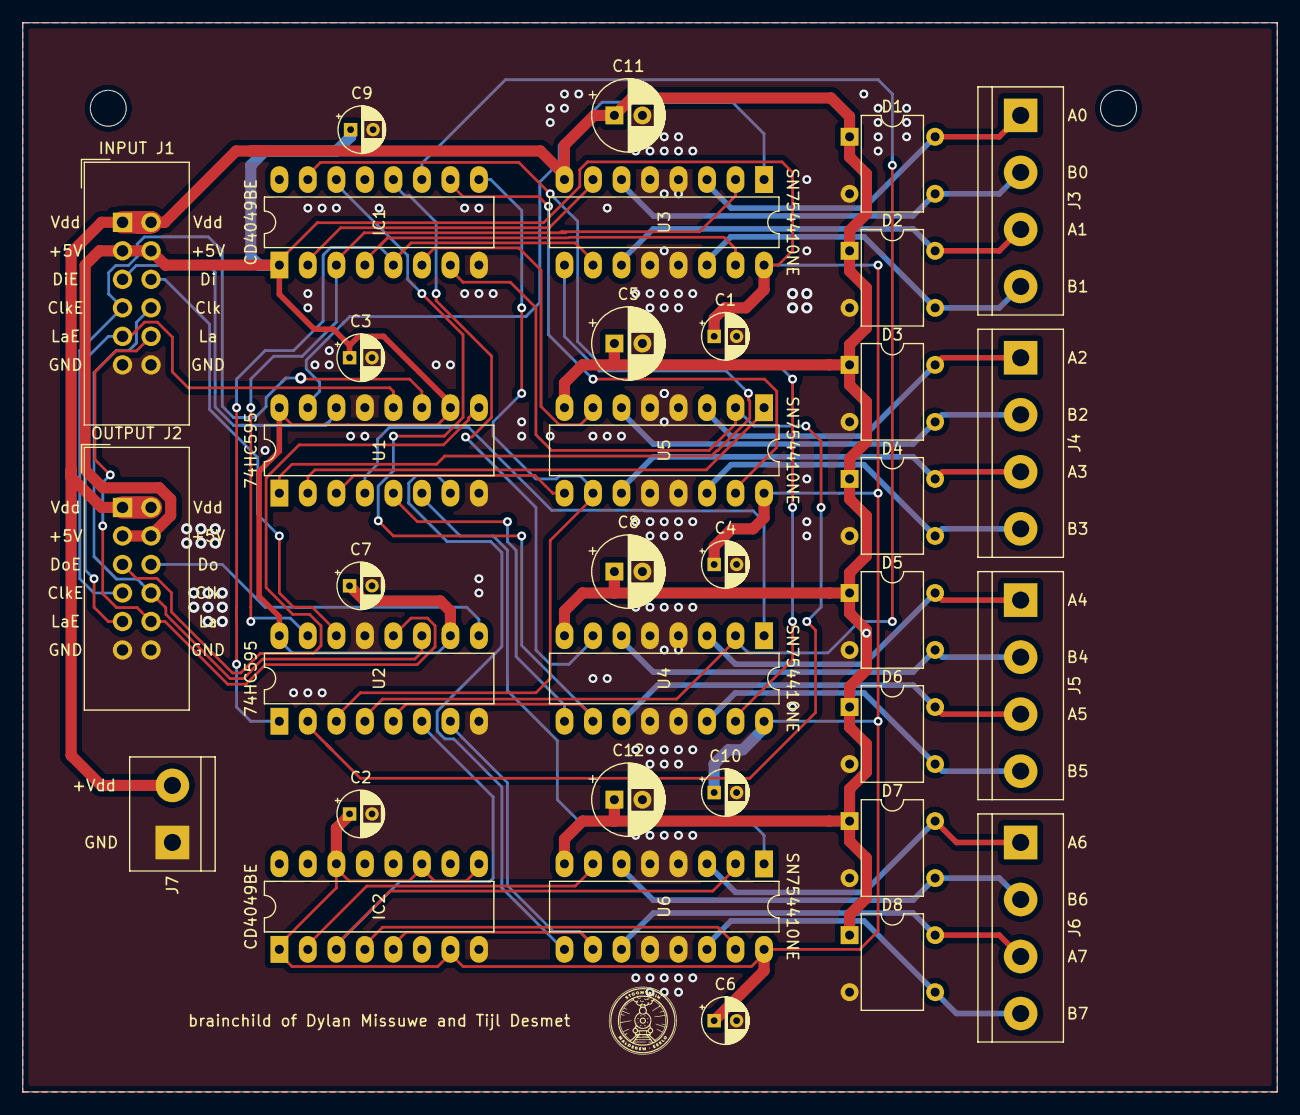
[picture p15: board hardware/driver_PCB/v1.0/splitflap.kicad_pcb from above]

Board: 2 copper layers, 111.8 x 95.2 mm, 35 parts (0 on the bottom side), 51 nets.

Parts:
C1, C2, C3, C4, C6, C7, C9, C10: CP; CP_Radial_D4.0mm_P2.00mm
C5, C8, C11, C12: CP; CP_Radial_D6.3mm_P2.50mm
D1, D2, D3, D4, D5, D6, D7, D8: D_Bridge_+-AA; Diode_Bridge_DIP-4_W7.62mm_P5.08mm
IC1, IC2: CD4049UBE; DIP-16_W7.62mm_LongPads
INPUT J1: Conn_02x06_Odd_Even; IDC-Header_2x06_P2.54mm_Vertical
J3, J4, J5, J6: Screw_Terminal_01x04; TerminalBlock_bornier-4_P5.08mm
J7: Screw_Terminal_01x02; TerminalBlock_bornier-2_P5.08mm
OUTPUT J2: Conn_02x06_Odd_Even; IDC-Header_2x06_P2.54mm_Vertical
U1, U2: 74HC595; DIP-16_W7.62mm_LongPads
U3, U4, U5, U6: SN754410NE; DIP-16_W7.62mm_LongPads

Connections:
GND: C1.2, C2.2, C3.2, C4.2, C5.2, C6.2, C7.2, C8.2, C9.2, C10.2, C11.2, C12.2, D1.2, D2.2, D3.2, D4.2, D5.2, D6.2, D7.2, D8.2, IC1.8, IC2.8, INPUT J1.11, INPUT J1.12, J7.1, OUTPUT J2.11, OUTPUT J2.12, U1.8, U1.13, U2.8, U2.13, U3.4, U3.5, U3.12, U3.13, U4.4, U4.5, U4.12, U4.13, U5.4, U5.5, U5.12, U5.13, U6.4, U6.5, U6.12, U6.13
unnamed: D1.3, J3.2, U3.6
unnamed: D1.4, J3.1, U3.3
unnamed: D2.3, J3.4, U3.14
unnamed: D2.4, J3.3, U3.11
unnamed: D3.3, J4.2, U5.6
unnamed: D3.4, J4.1, U5.3
unnamed: D4.3, J4.4, U5.14
unnamed: D4.4, J4.3, U5.11
unnamed: D5.3, J5.2, U4.6
unnamed: D5.4, J5.1, U4.3
unnamed: D6.3, J5.4, U4.14
unnamed: D6.4, J5.3, U4.11
unnamed: D7.3, J6.2, U6.6
unnamed: D7.4, J6.1, U6.3
unnamed: D8.3, J6.4, U6.14
unnamed: D8.4, J6.3, U6.11
unnamed: IC1.2, U3.7
unnamed: IC1.3, U2.15, U3.2
unnamed: IC1.4, U3.15
unnamed: IC1.5, U2.1, U3.10
unnamed: IC1.6, U5.7
unnamed: IC1.7, U2.2, U5.2
unnamed: IC1.9, U2.3, U5.10
unnamed: IC1.10, U5.15
unnamed: IC1.11, U2.4, U4.2
unnamed: IC1.12, U4.7
unnamed: IC1.14, U2.5, U4.10
unnamed: IC1.15, U4.15
unnamed: IC2.2, U6.7
unnamed: IC2.3, U2.6, U6.2
unnamed: IC2.4, U6.15
unnamed: IC2.5, U2.7, U6.10
unnamed: INPUT J1.5, U1.14
unnamed: INPUT J1.6, U2.14
unnamed: INPUT J1.7, OUTPUT J2.7, U1.11
unnamed: INPUT J1.8, OUTPUT J2.8, U2.11
unnamed: INPUT J1.9, OUTPUT J2.9, U1.12
unnamed: INPUT J1.10, OUTPUT J2.10, U2.12
unnamed: OUTPUT J2.5, U1.9
unnamed: OUTPUT J2.6, U2.9
unnamed: U1.1, U3.9
unnamed: U1.2, U5.1
unnamed: U1.3, U5.9
unnamed: U1.4, U4.1
unnamed: U1.5, U4.9
unnamed: U1.6, U6.1
unnamed: U1.7, U6.9
unnamed: U1.15, U3.1
VCC: C1.1, C2.1, C3.1, C4.1, C6.1, C7.1, C9.1, C10.1, IC1.1, IC2.1, IC2.7, IC2.9, IC2.11, IC2.14, INPUT J1.3, INPUT J1.4, OUTPUT J2.3, OUTPUT J2.4, U1.10, U1.16, U2.10, U2.16, U3.16, U4.16, U5.16, U6.16
VDD: C5.1, C8.1, C11.1, C12.1, D1.1, D2.1, D3.1, D4.1, D5.1, D6.1, D7.1, D8.1, INPUT J1.1, INPUT J1.2, J7.2, OUTPUT J2.1, OUTPUT J2.2, U3.8, U4.8, U5.8, U6.8

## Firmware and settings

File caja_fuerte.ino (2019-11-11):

// ================== Librerias ================== 
//    Keypad.h          - Permite utilizar el teclado de 4x3
//    LiquidCrystal.h   - Permite utilizar la pantalla LCD de 16x2
//    EEPROM.h          - Permite utilizar la EEPROM interna de la arduino mega
// ===============================================

#include <Keypad.h>
#include <LiquidCrystal.h>
#include <EEPROM.h>




// ===== Configuración del teclado =====
//         ---------------------    
//         | ARDUINO | TECLADO |
//         |---------|---------|
//         |   19    |    1    |
//         |   21    |    2    |
//         |   23    |    3    |
//         |   25    |    4    |
//         |   27    |    5    |
//         |   29    |    6    |
//         |   31    |    7    |
//         ---------------------
// =====================================

// Se define el tamaño del teclado: 4 filas y 3 columnas
const byte ROWS = 4; const byte COLS = 3;   

// Se define el tipo de dato que el sistema interpretara 
// al presionar la tecla.
char keys[ROWS][COLS] = {                   
    {'1','2','3'},
    {'4','5','6'},
    {'7','8','9'},
    {'N','0','Y'}
};

// Se define en cuales pines se encuentra conectado el teclado
byte rowPins[ROWS] = {19, 21, 23, 25};
byte colPins[COLS] = {27, 29, 31};

// Se pone en marcha el funcionamiento del teclado
Keypad keypad = Keypad( makeKeymap(keys), rowPins, colPins, ROWS, COLS );




// ===== Configuración de la pantalla =====
//         ---------------------    
//         | ARDUINO | PANTALLA |
//         |---------|----------|
//         |   GND   |    VSS   |
//         |   5V    |    VDD   |
//         |         |    VO    |
//         |   33    |    RS    |
//         |   GND   |    RW    |
//         |   35    |    E     |
//         |         |    D0    |
//         |         |    D1    |
//         |         |    D2    |
//         |         |    D3    |
//         |   37    |    D4    |
//         |   39    |    D5    |
//         |   41    |    D6    |
//         |   43    |    D7    |
//         |   5v    |    A     |
//         |   GND   |    K     |
//         ----------------------
// ======================================

// Se establecen los pines que estaran conectados
byte rs = 33, en = 35, d4 = 37, d5 = 39, d6 = 41, d7 = 43;
LiquidCrystal lcd(rs, en, d4, d5, d6, d7);




// ===== Configuraciones extras =================== 
// Se establecen otros pines que seran utilizados 
// ================================================

const byte PIN_LED_1           = 17;
const byte PIN_LED_2           = 15;
const byte PIN_LED_3           = 13;
const byte PIN_LED_4           = 11;
const byte PIN_LED_5           = 9;
const byte PIN_LED_PUERTA      = 7;
const byte PIN_LED_ALARMA      = 5;
const byte PIN_RELE_PUERTA     = 32;
const byte PIN_RELE_ALARMA     = 34;





// ===== Variables Globales =======================
// Estas son las variables que se utilizan en todo 
// el codigo, para manejar el flujo del programa.
// ================================================

// Estos variables se utilizan para controlar cuando un
// usuario puede entrar o salir de un modo.
bool controlInicio          = false;
bool controlPinAsignado     = false;
bool controlPinIngresado    = false;
bool controlCajaAbierta     = false;
bool controlAlarma          = false;

// Estas variables se leen de la EEPROM para realizar acciones.
bool opcPrimerInicio        = false;    // Permite acceder al cambio de pin 
bool opcEstadoAlarma        = false;    // Hace sonar la alarma
bool opcEstadoPin           = false;    // Abre la puerta

// Estas son variables en forma de array para almacenar 
// en la memoria RAM los pines
byte pinGuardado[6];
byte pinMemoria[6];

// Estas variables se utilizan para activar el modo programador
// al inicio de la caja fuerte.
int debugcode               = 0;
bool debugmode              = false;

// Estas son direcciones de memoria de la EEPROM. Se utiliza
// para almacenar y/o leer datos persistentes tras reinicios.
const byte dirPrimerInicio     = 0;
const byte dirNumIntentos      = 1;
const byte dirAlarma           = 2;
const byte dirCajaAbierta      = 3;
const byte dirPinGuardado      = 95; 

// Otras variables, se definen globalmente y tienen muchos usos.
byte pinX                   = 0;
byte intentos               = 0;





// ===== Función Inicial ==========================
// Se ejecuta una sola vez durante el inicio. Se 
// definen la configuración de los pines. Se inicia 
// la pantalla y el puerto serial.
// ================================================

void setup() {   
    // Inicializa el puerto serial para enviar información
    // hacia la computadora.
    Serial.begin(9600);
    while (!Serial) {
        ; 
    }
    
    // Inicializa la pantalla con el tamaño 16x02, limpia el
    // contenido de la misma y activa el parpadeo del cursor.
    // Tras eso muestra el mensaje de inicio.
    lcd.begin(16, 2);
    lcd.clear();
    lcd.blink();
    textoPreInicio();

    // Se establecen los pines extras como salida de datos.
    pinMode(PIN_LED_1,          OUTPUT);
    pinMode(PIN_LED_2,          OUTPUT);
    pinMode(PIN_LED_3,          OUTPUT);
    pinMode(PIN_LED_4,          OUTPUT);
    pinMode(PIN_LED_5,          OUTPUT);
    pinMode(PIN_LED_PUERTA,     OUTPUT);
    pinMode(PIN_LED_ALARMA,     OUTPUT);
    pinMode(PIN_RELE_ALARMA,    OUTPUT);
    pinMode(PIN_RELE_PUERTA,    OUTPUT);
}





// ===== Función Principal ======================== 
// Se ejecuta indefinidamente tras terminar la 
// funcion inicial. Se encarga de cambiar entre los
// distintos modos del sistema. Lee las direcciones
// de la EEPROM, guarda el dato en las variables
// de opcion y accede a un modo hasta que el valor
// de la variable de control cambie.
// ================================================

void loop() { 

    // Espera al usuario/programador a que comience
    // el programa presionando el boton cero.
    while (controlInicio == false) {
        controlInicio = modoComienzo();
    }
    textoInicio();


    // Carga desde la EEPROM, el numero de intentos
    // disponibles. Ilumina los correspondientes LEDS.
    intentos = EEPROM.read(dirNumIntentos);
    controlLeds(intentos, true);


    // Comprueba si la alarma deberia sonar, de ser asi
    // empieza a sonar la alarma y entra en el modo alarma.
    opcEstadoAlarma = EEPROM.read(dirAlarma);
    if (opcEstadoAlarma == true) {
       Serial.println(F("# Modo > Alarma sonando"));
        textoAlarma();

        controlLeds(7, true);
        digitalWrite(PIN_RELE_ALARMA, HIGH);
        while (controlAlarma == false) {
            controlAlarma = modoAlarma();
        }    
    } else {
        controlLeds(7, false);
        digitalWrite(PIN_RELE_ALARMA, LOW);
    }


    // Comprueba si es el primer inicio de la caja fuerte,
    // de ser asi entra en el modo nuevo pin. En caso contrario,
    // accederia al modo ingreso de pin.
    opcPrimerInicio = EEPROM.read(dirPrimerInicio);
    if (opcPrimerInicio == true) {

        // Muestra por serial y en pantalla el modo
        Serial.println(F("# Modo > Nuevo pin"));
        textoNuevoPin();            
      
        // Accede al modo nuevo pin
        while (controlPinAsignado == false) {
            controlPinAsignado = modoNuevoPin();
        }
   
        limpiarLCD();      

    } else {

        // Muestra por serial y en pantalla el modo
        Serial.println(F("# Modo > Ingreso de pin"));
        textoIngresePin();

        // Accede al modo ingreso de pin
        while (controlPinIngresado == false) {
            controlPinIngresado = modoIngresarPin();
        }
        
        limpiarLCD(); 

    }

    // Comprueba si el pin fue ingresado correctamente tras
    // entrar al modo ingreso de pin, de ser asi entra al 
    // modo de caja abierta.
    if (controlPinIngresado == true) {
        opcEstadoPin = EEPROM.read(dirCajaAbierta);
        if (opcEstadoPin == true) {
            // Muestra por serial y en pantalla el modo
           Serial.println(F("# Modo > Caja Abierta"));
            textoCajaAbierta();

            // Accede al modo caja abierta
            digitalWrite(PIN_RELE_PUERTA, HIGH);
            while (controlCajaAbierta == false) {
                controlCajaAbierta = modoCajaAbierta();
            }
        } else {
            digitalWrite(PIN_RELE_PUERTA, LOW);
        }
    }
}




// ===== Funciones de texto =============================================================
//  Dedicadas al texto e información almacenada:
//  -> textoPreInicio        - Muestra por serial y por LCD el mensaje de introduccion. 
//  -> textoNuevoPin     - Muestra por el LCD el mensaje de nuevo pin.
//  -> textoConfirmarPin - Muestra por el LCD el mensaje de confirmar pin.
//  -> textoIngresePin   - Muestra por el LCD el mensaje de ingrese pin.
//  -> textoAlarma       - Muestra por el LCD el mensaje de ingrese puk.
//  -> leerMemoriaPin    - Muestra por el Serial el pin almacenado en memoria.     
//  -> leerEEPROMPin     - Muestra por el Serial el pin almacenado en la EEPROM.
// ======================================================================================

void textoPreInicio() {  
   Serial.println(F("Bienvenido a la consola de la Caja Fuerte.\n"   )); 
   Serial.println(F("Presione cero para continuar.\n"                ));
    delay(50);

    limpiarLCD(); 
    escribirLCD(0, 0, " Presione cero  ");
    escribirLCD(0, 1, " para continuar ");  
}

void textoInicio() {
   Serial.println(F("# Modo > Inicio de caja fuerte"));
    delay(50);
}

void textoNuevoPin() {
    limpiarLCD();                     
    escribirLCD(0, 0, "Nuevo PIN:");   
    escribirLCD(0, 1, ">");
}

void textoConfirmarPin() {
    limpiarLCD();
    escribirLCD(0, 0, "    CONFIRMA    ");
    escribirLCD(0, 1, " No:[*]  Si:[#] ");
}

void textoIngresePin() {
    limpiarLCD();
    escribirLCD(0, 0, "Ingrese PIN:    ");
    escribirLCD(0, 1, ">");
}

void textoAlarma() {
    limpiarLCD();
    escribirLCD(0, 0, "Ingrese PUK:    ");
    escribirLCD(0, 1, ">");  
}

void textoCajaAbierta() {
    limpiarLCD();
    escribirLCD(0, 0, "Cerrar Caja [*] ");
    escribirLCD(0, 1, "Cambiar PIN [#] ");
}

void leerMemoriaPin() {
    Serial.print("Pin: ");
    for (int i = 0; i <= 5; i++) {  
        byte value = pinMemoria[i];
        Serial.write(value);
    } 
    Serial.println();   
}

void leerEEPROMPin() {
    Serial.print("Pin: ");
    for (int addr = 0; addr <= 5; addr++) {  
        byte value = EEPROM.read(addr + dirPinGuardado);
        Serial.write(value);
    } 
    Serial.println();   
}




//  ===== Funciones del LCD =============================================================
//  Controlan la pantalla LCD para escribir/borrar.
//  -> limpiarLCD        - Limpia todos los caracteres en el LCD.
//  -> escribirLCD       - Fija posicion y escribe texto.
//  -> escribirBinLCD    - Identico a writeLCD pero recibe texto en formato ASCII.
// ======================================================================================

void limpiarLCD() {
    escribirLCD(0, 0, "                "); 
    escribirLCD(0, 1, "                "); 
}

void escribirLCD(byte x, byte y, const char* txt) {
    lcd.setCursor(x, y);
    lcd.write(txt); 
}

void escribirBinLCD(byte x, byte y, byte txt) {
    lcd.setCursor(x, y);
    lcd.write(txt); 
}





// ===== Funciones de Pin ===============================================================
// Dedicadas a controlar datos del pin.
// -> teclaSerial         - Muestra por serial la tecla persionada en el teclado. 
// -> verificarPin        - Comprueba si el pin de memoria es igual al pin de la EEPROM. 
// -> guardarEEPROMPin    - Guarda el pin en memoria hacia la EEPROM.
// -> limpiarMemoriaPin   - Limpia el pin almacenado en memoria.
// ======================================================================================

void teclaSerial(byte texto) {    
    Serial.print(F("Tecla: "));
    Serial.write(texto);
    Serial.print(F(" - ")); 
    Serial.print(texto);
    Serial.println();    
}

bool verificarPin() {
    Serial.print("Comprobando pin: ");     
    byte pinMem;
    byte pinEEP;
    for (int j = 0; j <= 5; j++) {  
        pinEEP = EEPROM.read(j + dirPinGuardado);
        pinMem = pinMemoria[j];                   
        if (pinMem != pinEEP) {
           Serial.println(F("Pin incorrecto"));
            return false;
        }
    } 

    Serial.println(F("Pin correcto"));
    return true;
}

void guardarEEPROMPin() {
    // Toma el pin que se encuentre actualmente en la memoria y 
    // lo almacena en la EEPROM.
    for (int addr = 0; addr <= 5; addr++) {
        EEPROM.write(dirPinGuardado + addr, pinMemoria[addr]);
    }
    EEPROM.write(dirPrimerInicio, false);
}

void limpiarMemoriaPin() {
    // Limpia el pin guardado en memoria con un valor que el teclado
    // no puede ingresar, es decir la A.
    for (int i = 0; i <= 5; i++) {
        pinMemoria[i] = 65;
    } 
    pinX = 0;
}




// ===== Modos Internos =================================================================
// Son todas las funciones internas del programa
// -> modoNuevoPIN      - Utilizado para guardar un nuevo pin en la memoria eeprom.
// -> modoIngresarPin   - Permite acceder a la caja fuerte si cumple los controles de pin 
//                        e intentos. 
// -> modoCajaAbierta   - Permite cambiar la contraseña, cerrar la puerta con un boton o 
//                        un cierre automatico tras cinco min.
// -> modoAlarma        - Empieza a sonar la alarma y pide el codigo puk para desbloquear.
// -> modoComienzo      - Activa el modo de programador o inicia la caja fuerte
// -> modoProgramador   - Ejecuta comandos para configurar la caja
// ======================================================================================

bool modoNuevoPin() {
    // Comprueba si se esta recibiendo un nuevo caracter por el teclado
    // en caso de que lo haga, guarda este pin en la variable pinTecla.
    byte pinTecla = 0;
    pinTecla = keypad.getKey();
    if (pinTecla != NO_KEY){  
        // Imprime la tecla por el puerto serial
        teclaSerial(pinTecla);

        // Comprueba si la tecla ingresada se encuentra entre 0 y 9 (48-57 en ASCII) 
        if ((pinTecla >= 48) && (pinTecla <= 57)) {
            escribirBinLCD((pinX + 1), 1, pinTecla);
            pinMemoria[pinX] = pinTecla;
            pinX = pinX + 1;
            
            // Comprueba si ultimo pin ingresado es el sexto, si lo es guarda
            // el pin en la EEPROM y sale de la funcion nuevoPin().
            if (pinX == 6) {      
                delay(5000);      
                textoConfirmarPin();         
                bool pinConfirmado    = false;
                byte pinConfirmacion  = 0;
            
                // Mientras no haya sido confirmado
                while (pinConfirmado == false) {

                    // Comprueba el teclado y guarda la respuesta del usuario
                    pinConfirmacion = keypad.getKey();
                    if (pinConfirmacion != NO_KEY){
                        Serial.print("Tecla: ");
                        Serial.write(pinConfirmacion);
                        Serial.println();
        
                        // Realiza limpieza del pin y pantalla si la respuesta del 
                        // usuario es negativa. Guarda el pin en la EEPROM si la 
                        // respuesta es positiva.
                        switch (pinConfirmacion) {
                            case 78: // N - NO                     
                                // Muestra el mensaje de inicio
                                textoNuevoPin();
                                
                                // Limpia el pin guardado en memoria
                                limpiarMemoriaPin();

                                // Sale del mensaje de confirmacion
                                pinConfirmado = true;
                                break;
                            
                            case 89: // Y - SI
                                // Guarda el pin en la EEPROM
                                guardarEEPROMPin();
                                
                                // Limpia el pin guardado en memoria
                                limpiarMemoriaPin();

                                // Sale del mensaje de confirmacion
                                pinConfirmado = true;
                                break;
            
                            default:  // Otra tecla
                                // No hace nada y espera respuesta.
                                pinConfirmado = false;
                                break;
                        }
                    }
                }

                // Si el pin esta confirmado que salga del modo nuevo pin
                if (pinConfirmacion == 78) { 
                    return false; 
                } else {
                    return true;
                }
            }
        }   
    }
    // Continua en el modo nuevo pin.
    return false; 
}

bool modoIngresarPin() {
    // Comprueba si se esta recibiendo un nuevo caracter por el teclado
    // en caso de que lo haga, guarda este pin en la variable pinTecla.
    byte pinTecla = 0;
    pinTecla = keypad.getKey();
    if (pinTecla != NO_KEY) {
        // Imprime la tecla por el puerto serial
        teclaSerial(pinTecla);
        
        // Comprueba si la tecla ingresada se encuentra entre 0 y 9 (48-57 en ASCII) 
        if ((pinTecla >= 48) && (pinTecla <= 57)) {
            escribirBinLCD((pinX + 1), 1, pinTecla);
            pinMemoria[pinX] = pinTecla;
            pinX = pinX + 1;
            
            // Comprueba si ultimo pin ingresado es el sexto, si lo es guarda
            // el pin en la EEPROM y sale de la funcion ingresarPin().
            if (pinX == 6) {  
                pinX = 0;
            }
        }
        
        // Reinicia el pin introducido si se presiona [*]
        if (pinTecla == 78) {
            limpiarMemoriaPin();
            textoIngresePin();
            leerEEPROMPin();    
            
        }
        
        // Comprueba la veracidad del pin introducido si se presiona [#]
        if (pinTecla == 89) {
            bool pinVerificado = verificarPin();  
            
            // Carga el numero de intentos
            intentos = EEPROM.read(dirNumIntentos);
            Serial.print("Intentos: ");
            Serial.println(intentos);

            // Si el pin esta verificado abre la caja fuerte.
            if (pinVerificado == true) {  
                controlLeds(6, pinVerificado);
                intentos = 5;
                EEPROM.write(dirNumIntentos, intentos);
                EEPROM.write(dirCajaAbierta, true);
                EEPROM.write(dirAlarma, false);
                return true;
            } else {
                // Deshabilita el led verde
                controlLeds(6, pinVerificado);
                intentos -= 1;
                EEPROM.write(dirNumIntentos, intentos);
                controlLeds(intentos, pinVerificado);
                
            }

            // Resta un intento, si es cero suena alarma.
            if (intentos <= 0) {
                intentos = 0;
                EEPROM.write(dirNumIntentos, intentos);
                EEPROM.write(dirCajaAbierta, false);
                EEPROM.write(dirAlarma, true);
                controlLeds(7, pinVerificado);
                return true;
            } 
            
        }
    }
    // Continua en el modo de ingresar pin
    return false;
}

bool modoCajaAbierta() {
    // TODO: Cerrar puerta y 60 segundos cierre automatico
    // TODO: Cambiar PIN
    return false;
}

bool modoAlarma() {
    return false;
}
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

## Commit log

2019-11-10 Se modifico el documento y se agregaron fotoso
    [Caja Fuerte.fzz]
2019-11-11 Eliminados documentos. Arreglado estructura
    [caja-fuerte.kicad_pcb, caja-fuerte.sch]
